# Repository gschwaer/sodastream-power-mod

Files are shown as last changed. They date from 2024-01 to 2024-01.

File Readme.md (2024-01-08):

# SodaStream Power Mod

> Because the Internet of Things needed a smart soda maker.

There is (or was) a soda maker called "SodaStream Power". It has some buttons and LEDs and uses a servo to do the usual pushing motion that soda makers require. Mine was broken probably due to an [unfortunate design decision](#just-why--the-beginnings) (and me). So I thought: If I have to fix it by replacing the MCU either way, why not use a WIFI-enabled one? So I build a replacement PCB with an ESP8266. It even runs python! 😲

Disclaimer: It doesn't access the internet. But it could! -- But what for? Maybe I should blink the current time in morse code for each new soda, or add a cloud backend so I can better scale my soda making. 🤔😉

So what does it use WIFI for? Well, I can debug it remotely while it's standing in the kitchen. 😅

Otherwise it just does, well, make soda. Though I improved (imo) the [user interface](#ui-changes) a little.

> ℹ️ I did this project in 2019, but I rewrote the software and documentation in 2023, so some details might be lost to time.

## Hardware

The PCB was designed in KiCad and fabricated by JLCPCB in 2019.

Main components:
* MCU: `ESP8266-12F`
* I2C-Port-Expander: `PCF8574AN`
  * Note: The suffix `A` implies a different I2C base address than the version without the `A`. The non-`A` chip works as well (but needs a minor change in code). (Took me a few hours debugging before I realized I stared at the wrong data sheet.)
* 2x Hall Switch: `SI7205-B-00-IV`
* High Side Power Switch: `TPS22810DBVR`

### Known Design issues

1. In the first revision I made a mistake and wired the LEDs to $V_{in} = 6.5 V$ (with higher values for the current limiting resistor). I thought this way I could prevent wasting power in the $3.3 V$ regulator for the LED current. Yes, that was dumb, because the regulator is a linear regulator, so the resistor dumps the same amount of power. 🤦 But the LEDs wouldn't burden the regulator at least. Anyway, the actual problem was that the port expander did not have open drain ports. Instead, ports are actively driven to low and high ($3.3V$), so in the "off" state, the LEDs (+Resistor) would see $6.5V-3.3V = 3.2V$ and would just be dimmer. 😬 I fixed it by cutting a trace and botching a wire to have the LEDs use the $3.3V$ supply rail. I'm still using that version to date. In the KiCad project that mistake has been fixed. But I didn't reorder a PCB, so that change is untested.
2. I used the least sensible GPIOs (GPIO 0, 2) for IO. It worked ok in the end, though I later had a minor issue in micropython with PWM on GPIO2 after a soft reset, because GPIO2 is a boot select pin. But I was able to fix that in software and either way: in regular operation we don't soft reset.
3. I placed some components and traces beside the antenna. Probably not good, but works ok. There is unfortunately not much space for traces around this huge center cutout.

### Schematics

> ⚠️ Warning: The [KiCad project](./PCB/Sodastream/) was converted from an older KiCad version. I'm not sure if that worked ok.

For ease of use I made some screenshots of the schematics.

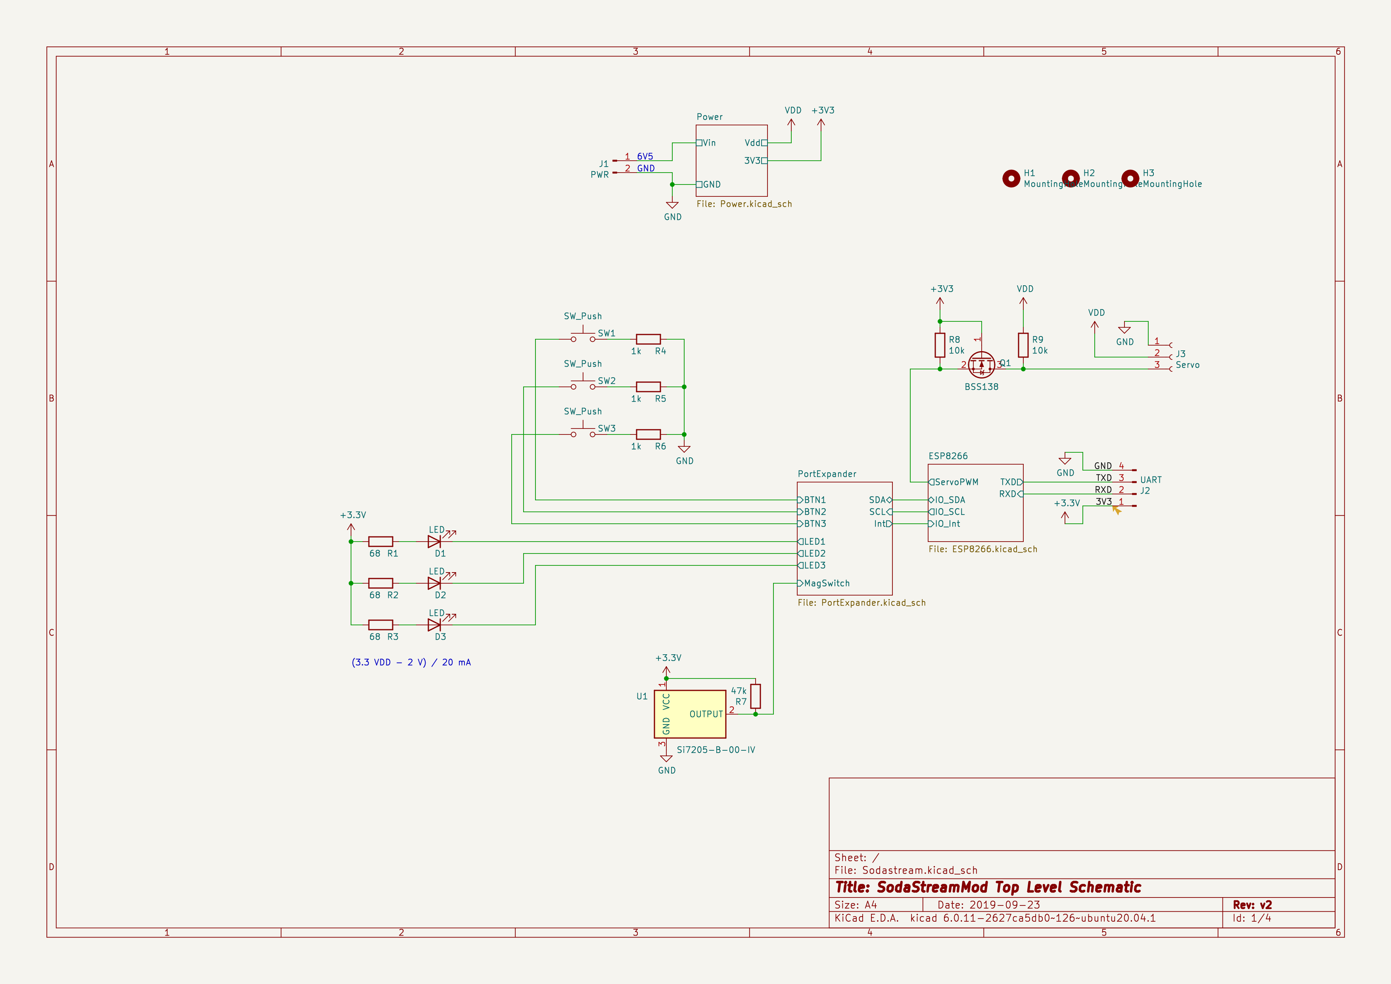
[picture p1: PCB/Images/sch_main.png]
main

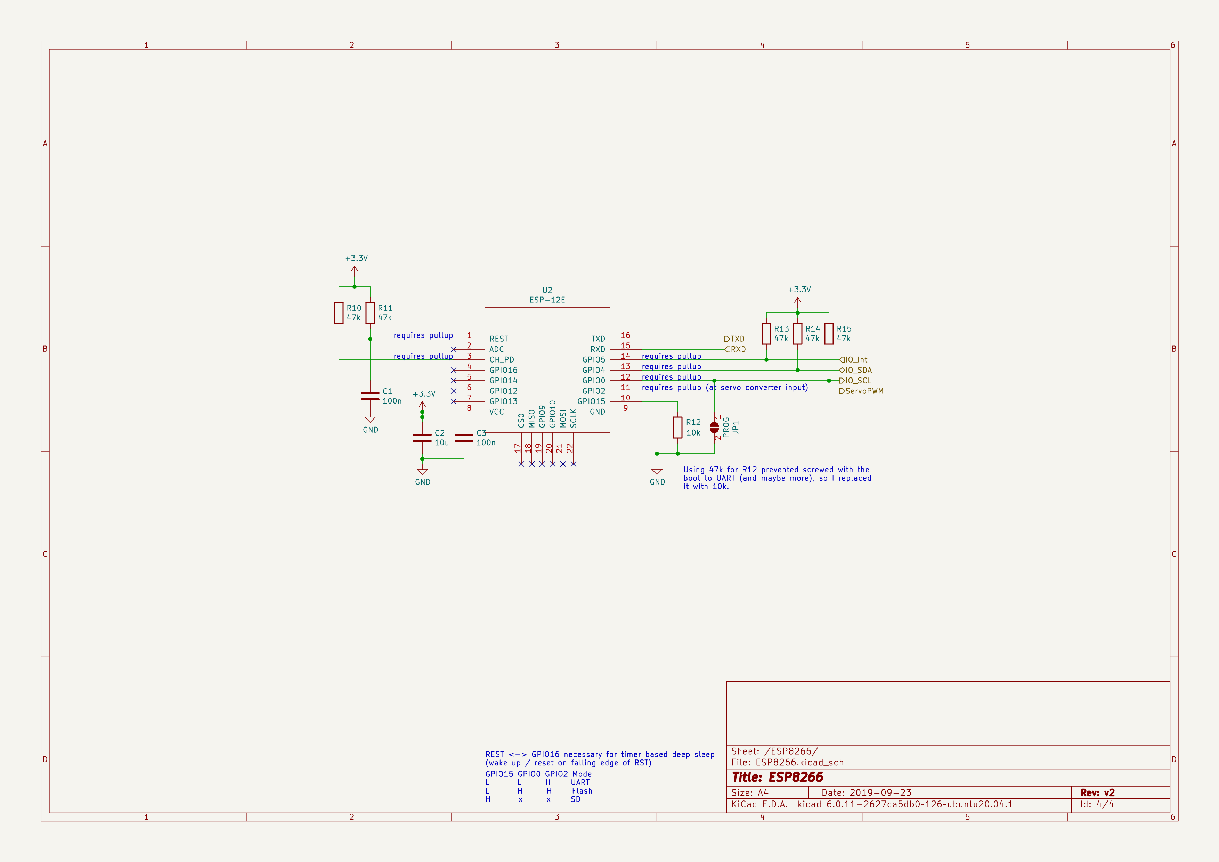
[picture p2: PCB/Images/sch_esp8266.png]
esp8266

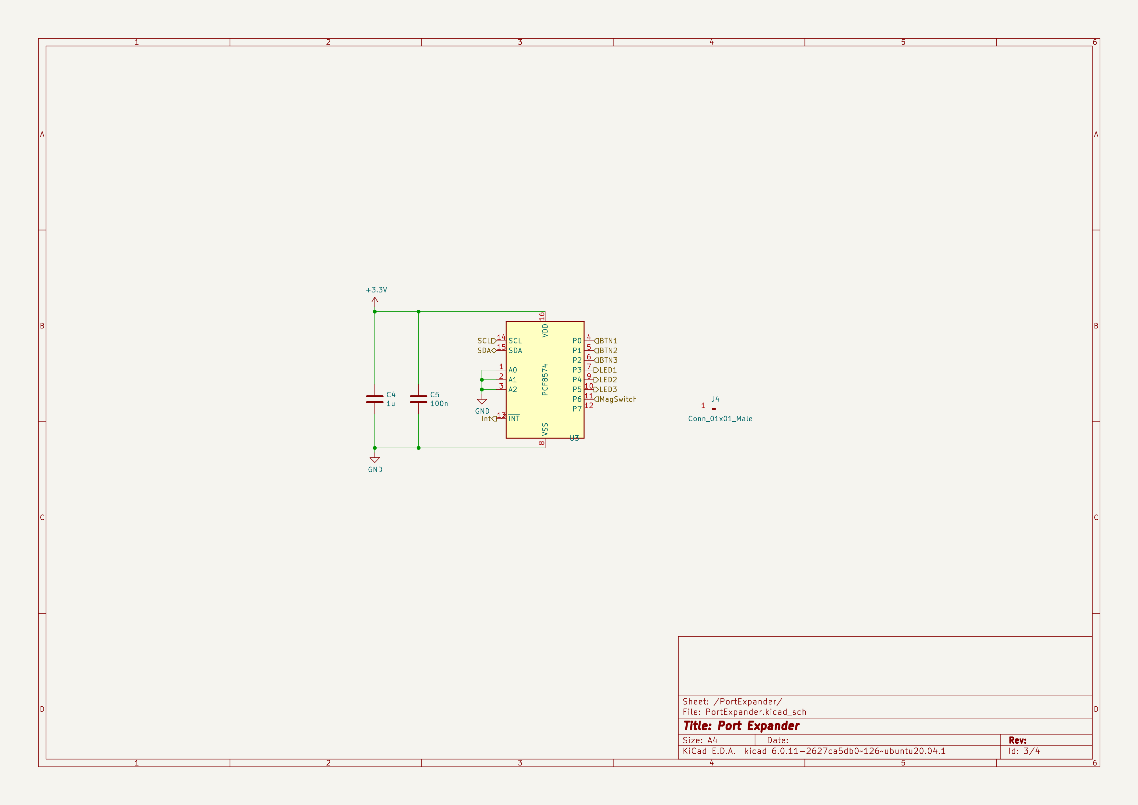
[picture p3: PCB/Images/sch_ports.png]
ports

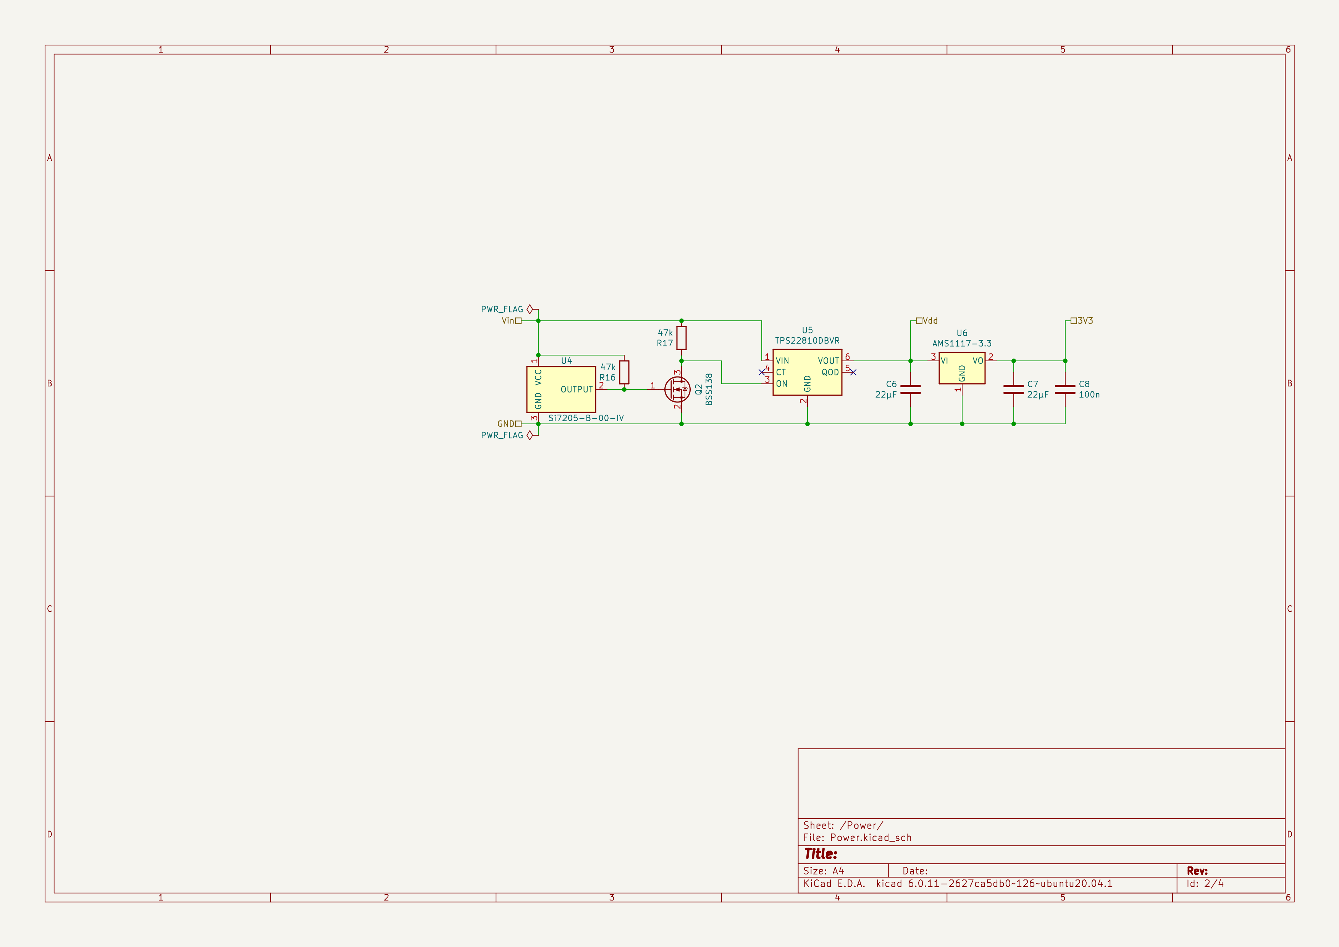
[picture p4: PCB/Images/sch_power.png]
power


### Layout

I measured the holes and cutouts on the original PCB and used identical ones on my PCB so it fits in the PCB holder. The pink areas are markings for special locations in the PCB housing: Left and right areas are keep out zones for the housing's snap fit hooks. The area in the center marks where the cabling leaves the water-proof housing.

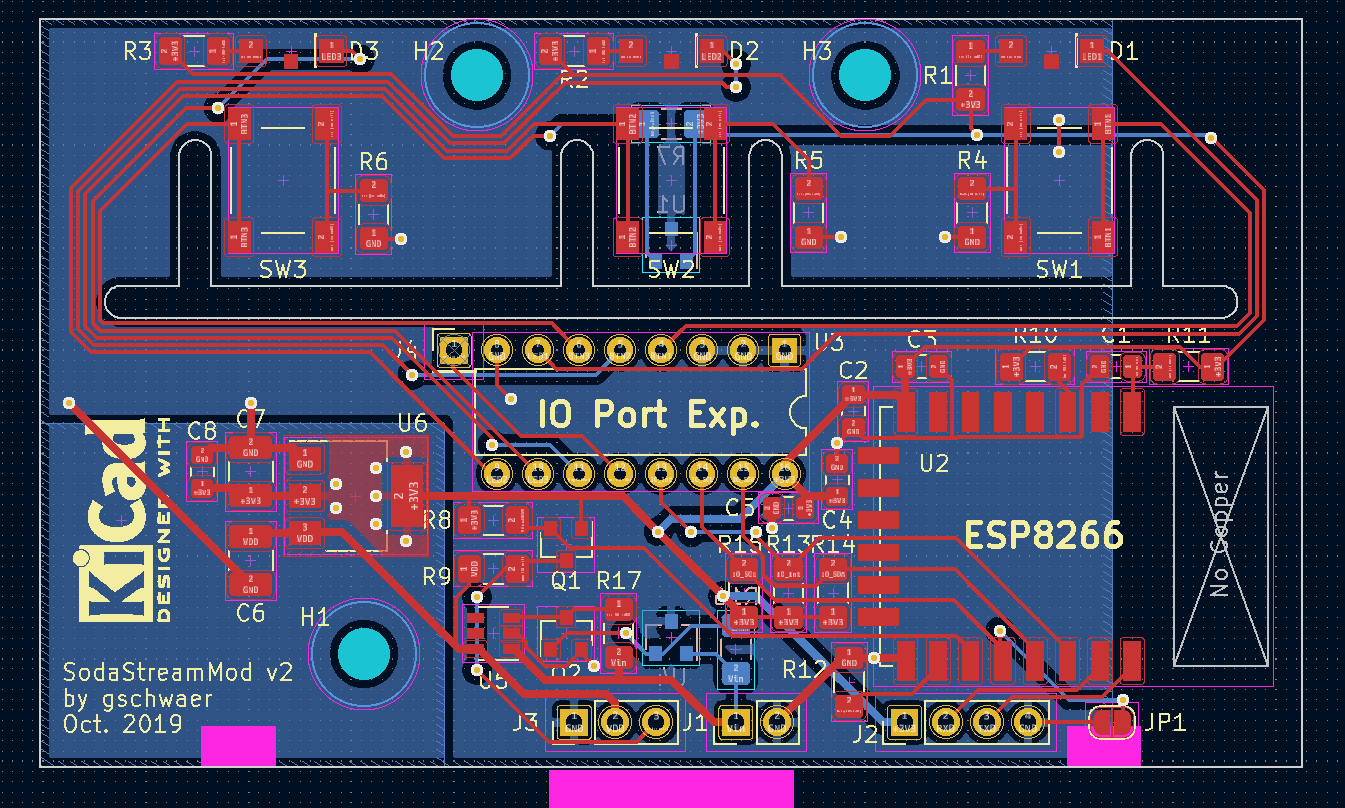
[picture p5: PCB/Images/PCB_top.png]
PCB_top

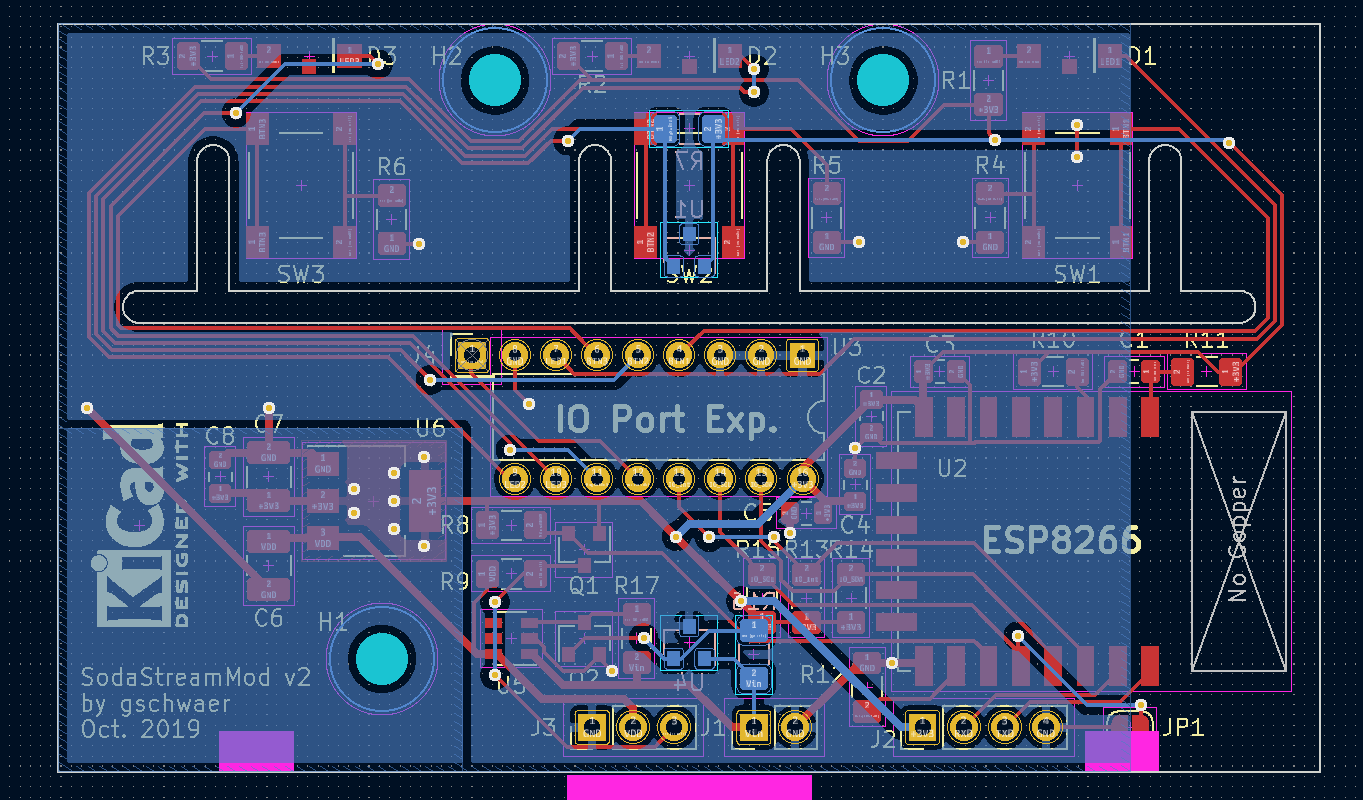
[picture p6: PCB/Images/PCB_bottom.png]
PCB_bottom

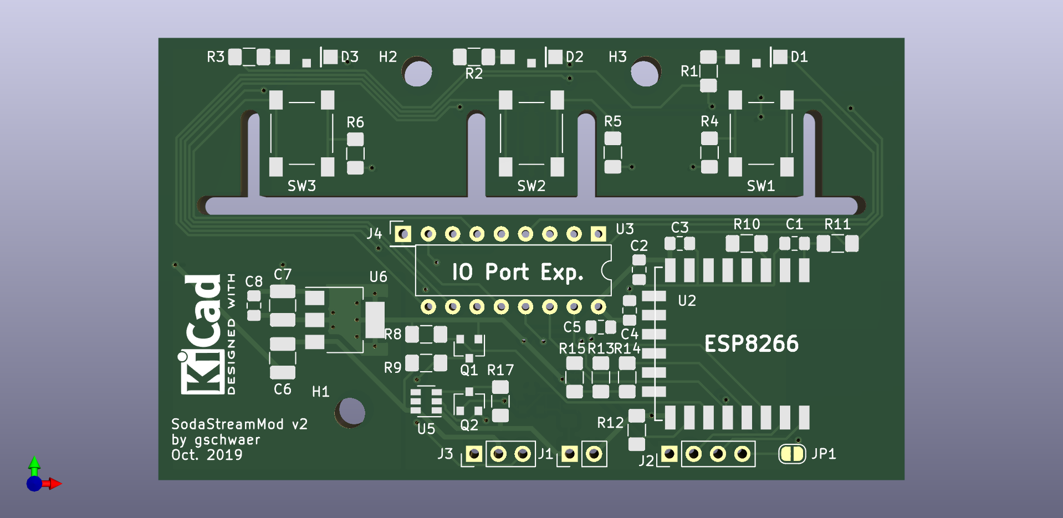
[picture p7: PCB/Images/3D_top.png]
render


## Software

This project uses [micropython](https://github.com/micropython/micropython/) version `1.20.0` installed as per the [documentation for ESP8266](https://docs.micropython.org/en/v1.20.0/esp8266/quickref.html). Here's the command I used:
```bash
esptool.py --port "${DEV}" --baud 460800 write_flash --erase-all --flash_size=detect 0 ESP8266_GENERIC-20230426-v1.20.0.bin
```
The code in [`./src`](./src/) is compiled with `make`. You need `mpy-cross`, `pyboard.py`, and `gcc` (see [`Makefile`](./src/Makefile)).

After that we can upload the code with [micropython's `pyboard.py` tool](https://docs.micropython.org/en/v1.20.0/reference/pyboard.py.html). The configs [`./src/webrepl_cfg.py`](./src/webrepl_cfg.py) and [`./src/wifi_cfg.py`](./src/wifi_cfg.py) require some adjustments.

After that, you can access the board via WiFi in the browser at http://192.168.0.123:8266/ (or which ever IP your board got, mDNS would be an improvement here, see [Future Work](#future-work)).

### UI Changes

Iirc the vendor UI was very basic: We have 3 buttons and 3 LEDs, when you insert a bottle all LEDs light up. Then you press one of the buttons, you get a low, medium, or high dose of CO2 into the bottle. The different doses are solely achieved by opening the CO2 valve for different, fixed durations.

Of course, that is reasonable, but it's actually a not much of an improvement compared to the manual soda makers. The main drawbacks are:
1. You still need to press a button,
2. when the CO2 cylinder empties, its pressure drops. This means the simple relationship between the duration of opening the valve and the applied CO2 dose does not hold anymore.

Drawback 1. is easily mitigated by beginning to open the CO2 valve as soon as a bottle is inserted. This means I cannot select the dose beforehand. This can be remedied by allowing a change of the dose *during* the operation. (This change is only in effect for the current soda making.)

I solved drawback 2. by tracking the cylinder state. I redefined the buttons to mean *left = "less CO2"*, *right = "more CO2"* (*center = "abort/restart"*). If a selection is made after the soda making is done, it is saved for next time. So when the CO2 cylinder empties, I can adjust the valve opening duration step by step whenever a bottle is not pressured to the degree I want. I also added some more subtle functions, and a debug mode:

| Button | Held Down Before* | Pressed While | Pressed After |
|---|---|---|---|
| left | (+right) reset cylinder state | less CO2 (temp) | less CO2 (saved) |
| right  | (+left) reset cylinder state  | more CO2 (temp) | more CO2 (saved) |
| middle | debug mode (WiFi) | abort | start again |

Table: Effect of buttons (1) held down while inserting a bottle, (2) pressed while the soda making happens, and (3) pressed after the soda making is completed. (* If any button is held down while a bottle is inserted, the CO2 valve stays closed. So resetting the cylinder state and entering debug mode can be done without wasting CO2.)

### Issues

I ran into some issues:

WebREPL:
* It's annoying to figure out the boards IP address. I currently check my router. But mDNS would be an obvious improvement.
* I regularly forget that when logging in via WebREPL, my python code is still running. Remember: after logging in, do `ctrl+c` to end the running program.

Boot Time:
* Boot time increases every time you overwrite a python file that is loaded at boot! I assume that has something to do with the flash filesystem trying to prevent wear. Maybe it does some copy-on-write with a linked list to traverse to the latest valid chunk? idk
  * If I remember correctly (! I didn't confirm it again !), you can reset this behavior by reformatting the flash (after that you have to reupload all files):
    ```python
    import uos
    from flashbdev import bdev
    uos.VfsLfs2.mkfs(bdev)
    vfs = uos.VfsLfs2(bdev)
    uos.mount(vfs, "/")
    ```
* I am using the following boot flow: `boot.py` -...-> `main.py` -> `sprudler.mpy`. That is mainly because `boot.py` and `main.py` cannot be compiled `.mpy` files. In `boot.py` I only put everything that I want done ASAP and `main.py` only `import`s the compiled `.mpy` file. I experimented a lot while trying to bring down boot time. I did not save the experiment results, but this solution got the best results for my use-case.
* The servo has three positions: (1) valve closed & bottle unlocked, (2) valve closed & bottle locked, (3) valve open & bottle locked. In `boot.py` I move the servo to the second (2) position. While the servo is moving to that position, we load the rest of the software and regular operation begins. This reduces the effective delay until operation begins.
* To optimize the compiled `.mpy` file, I experimented with regular global constants, constants marked with `const()`, and plain inserted constants. I'm not entirely sure what worked best, because while experimenting I also stumbled upon the issue above. Iirc boot time was best with inserted constants. So I stuck with that and added a preprocessor step using regular C preprocessor defines like `#define MY_CONST 123` in `sprudler.py`. (They get slightly garbled by the `black` formatter, but meh, I just undo this in the `Makefile`. Not elegant but works ok.)

WiFi AP:
* The WiFi AP does not work on my board with micropython `1.20.0`, so I disabled it (see [issue](https://github.com/micropython/micropython/issues/9226#issuecomment-1718269312)).
  * To prevent the board from boot looping after flashing, connect via serial and spam-paste the following into the terminal (including the newline):
    ```
    import network; network.WLAN(network.AP_IF).active(False)

    ```
    After some tries it will hit after the REPL becomes ready but before the AP is set up and the boot loop stops.

PWM:
* The servo is twitching if WiFi is enabled: The ESP8266 does not have hardware PWM outputs, so micropython does software PWM. WiFi will add a lot of load, which adds occasional lag on the software PWM timer handler. Ok for me, I only use WiFi in debug mode, where I can live with some servo twitching.

## Just Why?! / The Beginnings

Why am I doing this? Well, the electronics of my soda maker "broke", here's what happened:

The original circuitry has a tilt switch. It is just a conductive ball resting on two parallel wires, thus shorting the connection. The whole thing is in a black rectangular plastic housing with enough head room so the ball can slightly move upwards. If the PCB is flipped upside down the ball will fall away from the wires (now an open circuit) and the MCU will register that.

It turns out, if the device is on, you flip it upside down, and press any button, the MCU will go into an error state and blink the LEDs. Okay fine, maybe we just don't want our precious soda on the floor. But there is **no** way to get out of this error state! Not power cycling, no combination of button presses, short and long presses, with or without a bottle inserted, I tried everything I could think of. So ... this device just bricks itself? 🙃

Side note: If you are that kind of person (like me) who wants to know how devices work, and like to open them up to find out, you sometimes move parts aside, like for example **the PCB**, and maybe even let it dangle **upside down** on the side since the cables are so short...

However, I cannot be 100% certain that this is what bricked it. But there is a tilt switch on the PCB, it's connected to the controller, and the device went into the error state once I operated it with the PCB hanging upside down. But it could have been something else I did, who knows.

Why would the manufacturer do that? Not sure, maybe it is due to a regulation? CO2 in compressed gas cylinders is actually liquid. So from what I read, if you operate the valve while the CO2 cylinder is upside down it will spill the liquid CO2 which is very cold due to the drop in pressure. Maybe they wanted (or had) to prevent this hazard. (But why permanently!?)

## Future Work

- Add mDNS, so I don't need to look up the IP address.
  - https://github.com/vaudric/micropython/tree/main/mdns
  - https://github.com/nickovs/slimDNS
- Measure bottle pressure with a pressure sensor?

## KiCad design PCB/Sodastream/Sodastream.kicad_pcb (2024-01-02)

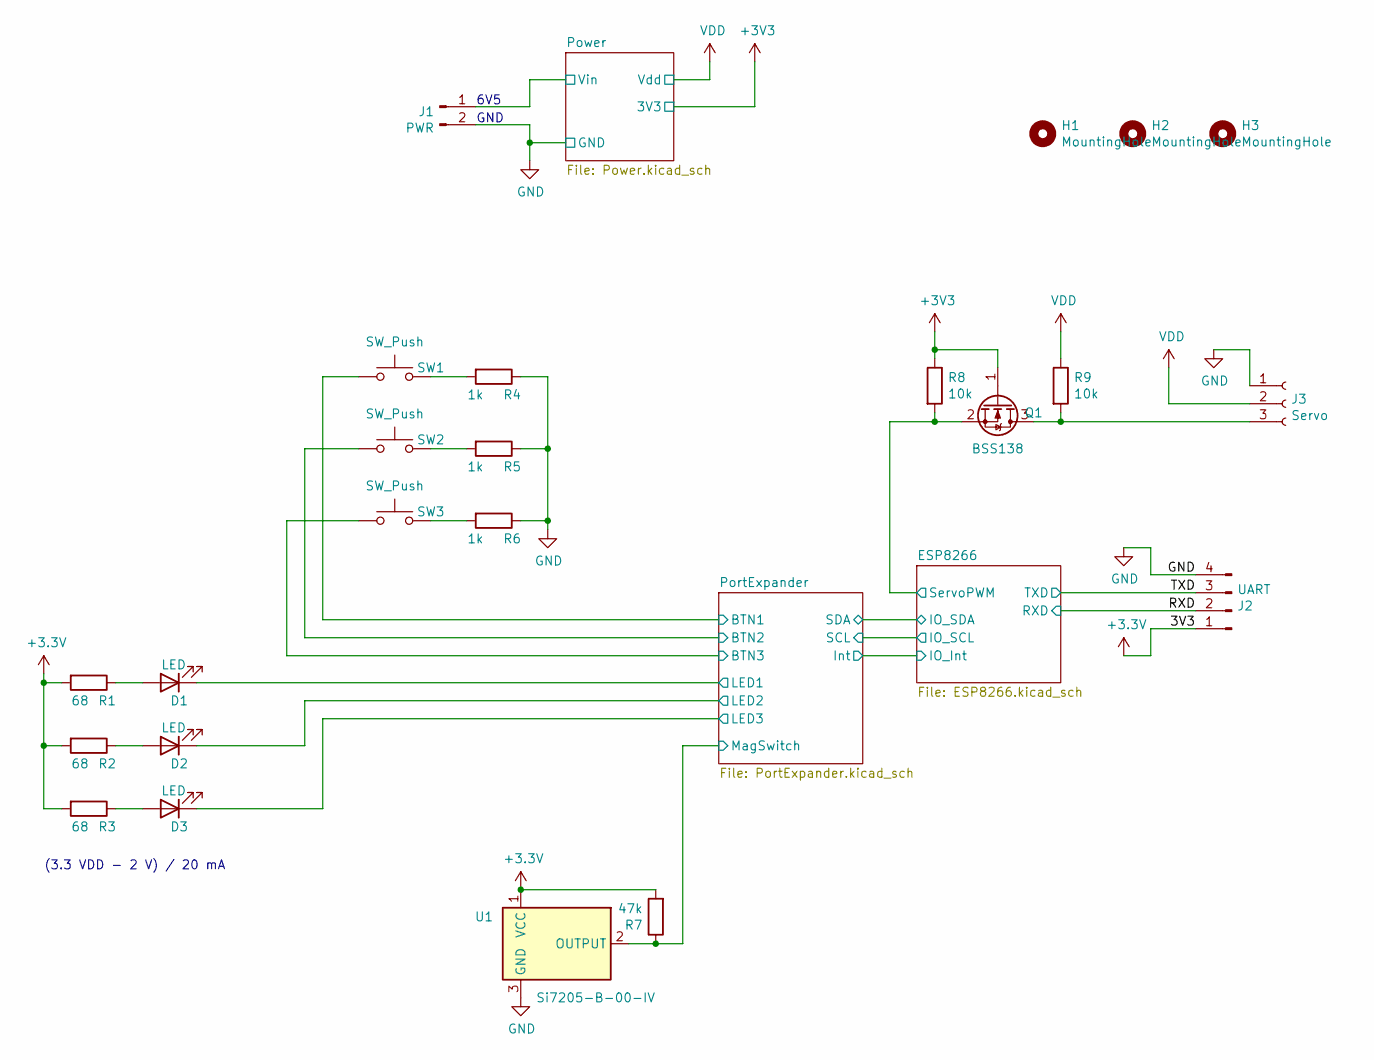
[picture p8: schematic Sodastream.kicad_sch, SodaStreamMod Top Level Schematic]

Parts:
D1, D2, D3: LED; LED_SMD_SideView_3.0x1.0x2.0_2+1pin
H1, H2, H3: MountingHole; MountingHole_3.2mm_M3
J1: PWR; PinHeader_1x02_P2.54mm_Vertical
J2: UART; PinHeader_1x04_P2.54mm_Vertical
J3: Servo; PinHeader_1x03_P2.54mm_Vertical
Q1: BSS138; SOT-23
R1, R2, R3: 68; R_1206_3216Metric_Pad1.42x1.75mm_HandSolder
R4, R5, R6: 1k; R_1206_3216Metric_Pad1.42x1.75mm_HandSolder
R7: 47k; R_1206_3216Metric_Pad1.42x1.75mm_HandSolder
R8, R9: 10k; R_1206_3216Metric_Pad1.42x1.75mm_HandSolder
SW1, SW2, SW3: SW_Push; SW_WE_6x6mm
U1: Si7205-B-00-IV; SOT-23

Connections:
+3V3: J2.1, Q1.1 (G), R1.2, R2.2, R3.2, R7.2, R8.1, U1.1 (VCC); also elsewhere on the board
/ESP8266/ServoPWM: Q1.2 (S), R8.2; also elsewhere on the board
/PortExpander/BTN1: SW1.1; also elsewhere on the board
/PortExpander/BTN2: SW2.1; also elsewhere on the board
/PortExpander/BTN3: SW3.1; also elsewhere on the board
/PortExpander/LED1: D1.1 (K); also elsewhere on the board
/PortExpander/LED2: D2.1 (K); also elsewhere on the board
/PortExpander/LED3: D3.1 (K); also elsewhere on the board
/PortExpander/MagSwitch: R7.1, U1.2 (OUTPUT); also elsewhere on the board
/Power/Vin: J1.1; also elsewhere on the board
/RXD: J2.2; also elsewhere on the board
/TXD: J2.3; also elsewhere on the board
GND: J1.2, J2.4, J3.1, R4.1, R5.1, R6.1, U1.3 (GND); also elsewhere on the board
unnamed: D1.2 (A), R1.1
unnamed: D2.2 (A), R2.1
unnamed: D3.2 (A), R3.1
unnamed: J3.3, Q1.3 (D), R9.2
unnamed: R4.2, SW1.2
unnamed: R5.2, SW2.2
unnamed: R6.2, SW3.2
VDD: J3.2, R9.1; also elsewhere on the board

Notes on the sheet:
(3.3 VDD - 2 V) / 20 mA
GND
6V5

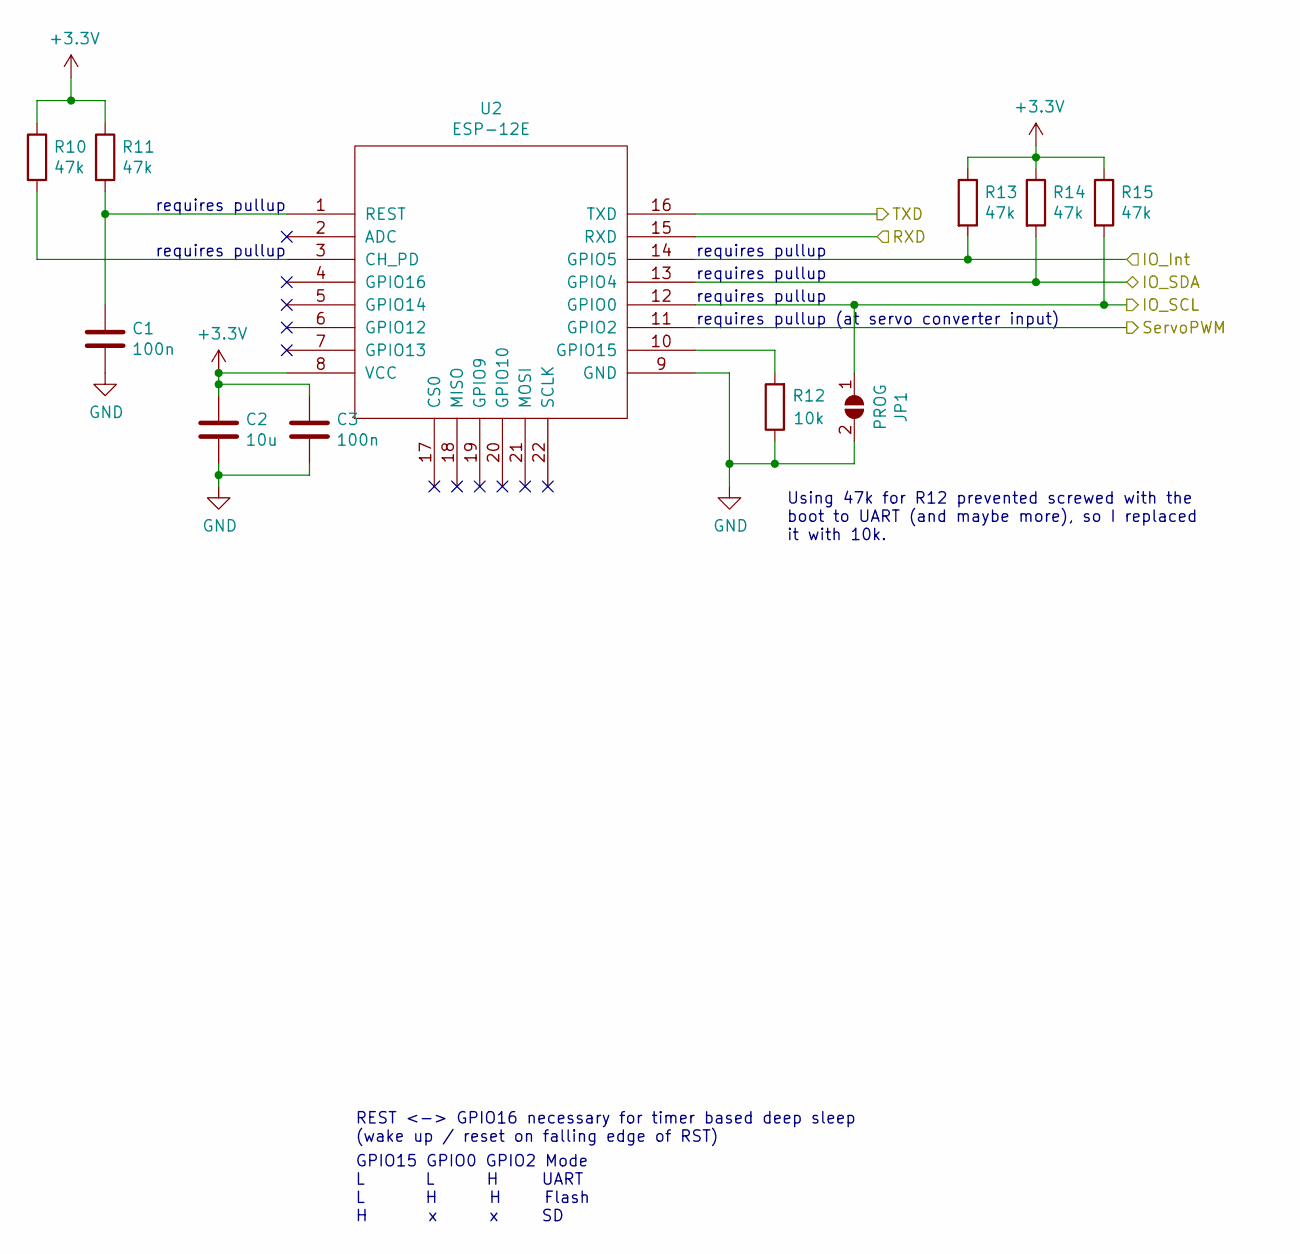
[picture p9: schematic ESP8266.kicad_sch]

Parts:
C1, C3: 100n; C_0805_2012Metric_Pad1.15x1.40mm_HandSolder
C2: 10u; C_0805_2012Metric_Pad1.15x1.40mm_HandSolder
JP1: PROG; SolderJumper-2_P1.3mm_Open_RoundedPad1.0x1.5mm
R10, R11, R13, R14, R15: 47k; R_1206_3216Metric_Pad1.42x1.75mm_HandSolder
R12: 10k; R_1206_3216Metric_Pad1.42x1.75mm_HandSolder
U2: ESP-12E; ESP-12E_SMD

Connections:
+3V3: C2.1, C3.1, R10.1, R11.1, R13.1, R14.1, R15.1, U2.8 (VCC); also elsewhere on the board
/ESP8266/IO_Int: R13.2, U2.14 (GPIO5); also elsewhere on the board
/ESP8266/IO_SCL: JP1.1 (A), R15.2, U2.12 (GPIO0); also elsewhere on the board
/ESP8266/IO_SDA: R14.2, U2.13 (GPIO4); also elsewhere on the board
/ESP8266/ServoPWM: U2.11 (GPIO2); also elsewhere on the board
/RXD: U2.15 (RXD); also elsewhere on the board
/TXD: U2.16 (TXD); also elsewhere on the board
GND: C1.2, C2.2, C3.2, JP1.2 (B), R12.1, U2.9 (GND); also elsewhere on the board
unnamed: C1.1, R11.2, U2.1 (REST)
unnamed: R10.2, U2.3 (CH_PD)
unnamed: R12.2, U2.10 (GPIO15)

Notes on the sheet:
requires pullup
requires pullup (at servo converter input)
Using 47k for R12 prevented screwed with the boot to UART (and maybe more), so I replaced it with 10k.
REST <-> GPIO16 necessary for timer based deep sleep (wake up / reset on falling edge of RST)
GPIO15 GPIO0 GPIO2 Mode L L H UART L H H Flash H x x SD

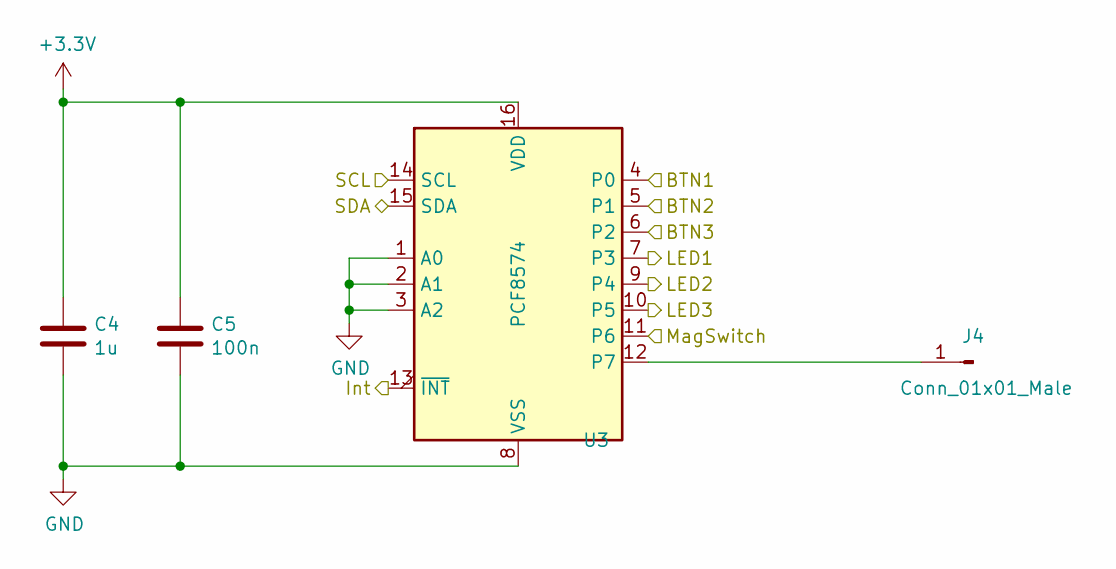
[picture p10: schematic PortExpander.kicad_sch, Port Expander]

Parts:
C4: 1u; C_0805_2012Metric_Pad1.15x1.40mm_HandSolder
C5: 100n; C_0805_2012Metric_Pad1.15x1.40mm_HandSolder
J4: Conn_01x01_Male; PinHeader_1x01_P2.54mm_Vertical
U3: PCF8574; DIP-16_W7.62mm

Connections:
+3V3: C4.1, C5.1, U3.16 (VDD); also elsewhere on the board
/ESP8266/IO_Int: U3.13 (~INT); also elsewhere on the board
/ESP8266/IO_SCL: U3.14 (SCL); also elsewhere on the board
/ESP8266/IO_SDA: U3.15 (SDA); also elsewhere on the board
/PortExpander/BTN1: U3.4 (P0); also elsewhere on the board
/PortExpander/BTN2: U3.5 (P1); also elsewhere on the board
/PortExpander/BTN3: U3.6 (P2); also elsewhere on the board
/PortExpander/LED1: U3.7 (P3); also elsewhere on the board
/PortExpander/LED2: U3.9 (P4); also elsewhere on the board
/PortExpander/LED3: U3.10 (P5); also elsewhere on the board
/PortExpander/MagSwitch: U3.11 (P6); also elsewhere on the board
GND: C4.2, C5.2, U3.1 (A0), U3.2 (A1), U3.3 (A2), U3.8 (VSS); also elsewhere on the board
unnamed: J4.1, U3.12 (P7)

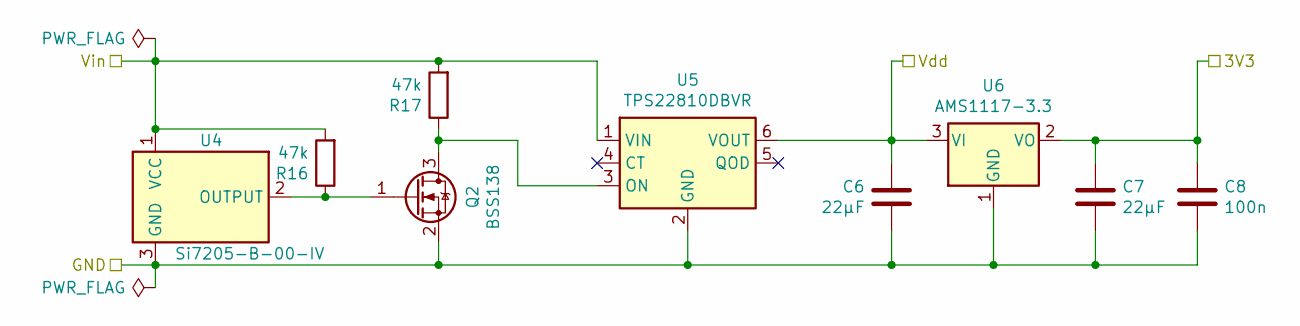
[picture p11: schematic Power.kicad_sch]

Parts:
C6, C7: 22µF; C_1210_3225Metric_Pad1.42x2.65mm_HandSolder
C8: 100n; C_0805_2012Metric_Pad1.15x1.40mm_HandSolder
Q2: BSS138; SOT-23
R16, R17: 47k; R_1206_3216Metric_Pad1.42x1.75mm_HandSolder
U4: Si7205-B-00-IV; SOT-23
U5: TPS22810DBVR; SOT-23-6
U6: AMS1117-3.3; SOT-223-3_TabPin2

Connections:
+3V3: C7.1, C8.1, U6.2 (VO); also elsewhere on the board
/Power/Vin: R16.2, R17.2, U4.1 (VCC), U5.1 (VIN); also elsewhere on the board
GND: C6.2, C7.2, C8.2, Q2.2 (S), U4.3 (GND), U5.2 (GND), U6.1 (GND); also elsewhere on the board
unnamed: Q2.1 (G), R16.1, U4.2 (OUTPUT)
unnamed: Q2.3 (D), R17.1, U5.3 (ON)
VDD: C6.1, U5.6 (VOUT), U6.3 (VI); also elsewhere on the board

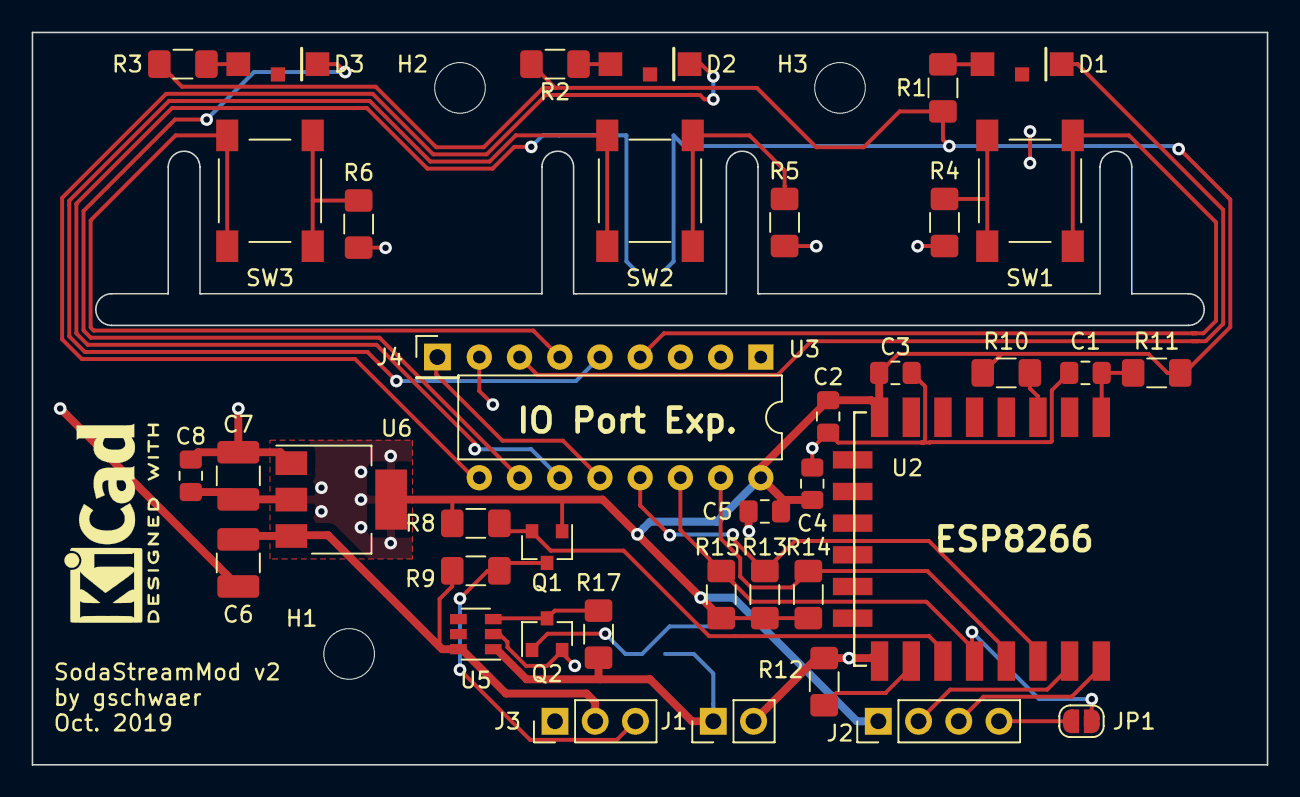
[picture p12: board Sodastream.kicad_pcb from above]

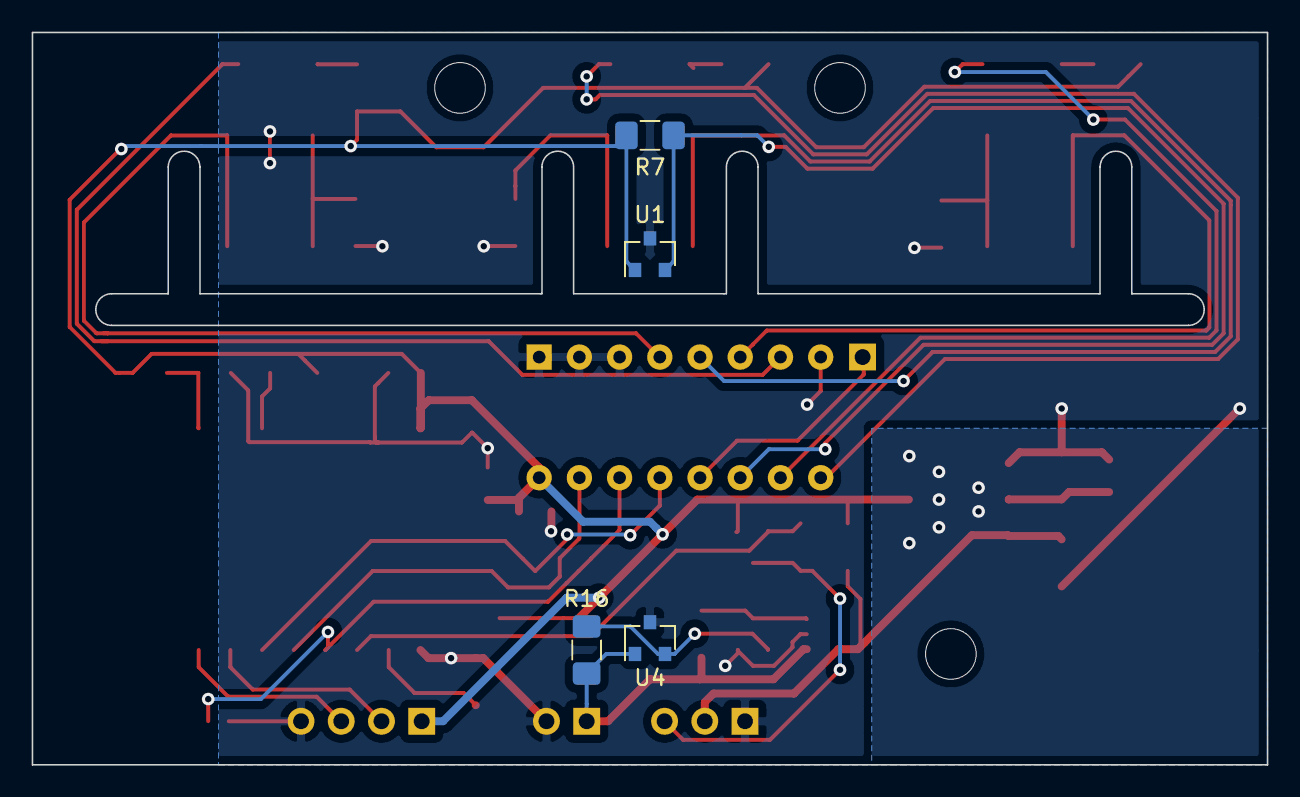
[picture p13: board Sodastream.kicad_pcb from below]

Board: 2 copper layers, 78.0 x 46.2 mm, 47 parts (4 on the bottom side), 30 nets.

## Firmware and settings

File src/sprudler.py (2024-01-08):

# Test with:
# ./pyboard.py -d /dev/serial/by-id/usb-1a86_USB_Serial-if00-port0 sprudler.py
# Build with:
# ../../micropython/mpy-cross/build/mpy-cross -march=xtensa -O3 ./sprudler.py
# Upload with:
# ./pyboard.py -d /dev/serial/by-id/usb-1a86_USB_Serial-if00-port0 -f cp sprudler.py :sprudler.py
# (beware, `import` prioritizes .py files over .mpy files)

import machine
import uasyncio
import time


# Setup servo

# define SERVO_PIN 2
# define SERVO_PWM_OPEN 50
# define SERVO_PWM_CLOSED 74
# define SERVO_PWM_ACTION 103

servo_pwm = machine.PWM(machine.Pin(SERVO_PIN), freq=50, duty=SERVO_PWM_CLOSED)
# servo_pwm.deinit()  # Workaround for broken PWM after soft-reset
# servo_pwm = machine.PWM(machine.Pin(SERVO_PIN), freq=50, duty=SERVO_PWM_CLOSED)


# Setup port extender

# define PORT_EXT_PIN_SCL 0
# define PORT_EXT_PIN_SDA 4
# define PORT_EXT_PIN_INT 5
# define PORT_EXT_I2C_FREQ 100000
# define PORT_EXT_I2C_ADDR 0b0111000
# define PORT_EXT_I2C_DFLT 0xFF

i2c = machine.I2C(
    scl=machine.Pin(PORT_EXT_PIN_SCL, machine.Pin.IN),
    sda=machine.Pin(PORT_EXT_PIN_SDA, machine.Pin.IN),
    freq=PORT_EXT_I2C_FREQ,
)
i2c_buf = bytearray(1)  # static buffer

# Setup button callback

# define BUTTON_LEFT 0
# define BUTTON_MID 1
# define BUTTON_RIGHT 2

btn_changed_flag = uasyncio.ThreadSafeFlag()
btn_pressed_mask = 0
btn_released_mask = 0


def button_callback(_pin):
    global btn_pressed_mask
    global btn_released_mask

    i2c.readfrom_into(PORT_EXT_I2C_ADDR, i2c_buf)
    btn_up_mask = i2c_buf[0] & 0x7
    # only buttons that were pressed are marked as now released
    btn_released_mask |= btn_up_mask & btn_pressed_mask
    btn_pressed_mask |= 0b111 ^ btn_up_mask  # same as ~btn_up_mask & 0x7

    btn_changed_flag.set()


ext_int = machine.Pin(PORT_EXT_PIN_INT, machine.Pin.IN)
ext_int.irq(trigger=machine.Pin.IRQ_FALLING, handler=button_callback)

# Setup LEDs
led_state = PORT_EXT_I2C_DFLT


def switch_leds(on_bits):
    global led_state

    led_state = (led_state & 0b11000111) | ((0b111 ^ on_bits) << 3)
    i2c_buf[0] = led_state
    i2c.writeto(PORT_EXT_I2C_ADDR, i2c_buf)


# Setup state

# define STATE_DEBUG -1
# define STATE_IDLE 0
# define STATE_ACTION 1
# define STATE_WAITING 2

state = STATE_IDLE
state_since = time.ticks_ms()
state_changed_event = uasyncio.Event()


def change_state(target_state):
    global state
    global state_since

    state = target_state
    state_since = time.ticks_ms()
    state_changed_event.set()
    state_changed_event.clear()


# Initial state
i2c.readfrom_into(PORT_EXT_I2C_ADDR, i2c_buf)
btn_up_mask = i2c_buf[0] & 0x7
if btn_up_mask == 0b111:  # no button pressed
    change_state(STATE_ACTION)
else:
    if btn_up_mask == 0b010:  # left and right button pressed
        import os

        try:
            os.remove("settings.cfg")
        except OSError:
            pass  # file does not exist

        switch_leds(111)
        time.sleep_ms(200)
        switch_leds(000)
        time.sleep_ms(200)
        switch_leds(111)
        time.sleep_ms(200)
        switch_leds(000)

        servo_pwm.duty(SERVO_PWM_OPEN)

        change_state(STATE_IDLE)
    else:  # middle button pressed
        change_state(STATE_DEBUG)

    # Wait until all buttons are unpressed
    while True:
        i2c.readfrom_into(PORT_EXT_I2C_ADDR, i2c_buf)
        btn_up_mask = i2c_buf[0] & 0x7
        if btn_up_mask == 0b111:  # no button pressed
            break

        time.sleep_ms(100)

    btn_pressed_mask = 0
    btn_released_mask = 0


# Coroutines


async def button_handler():
    global btn_pressed_mask
    global btn_released_mask
    global state
    global pump_dur_ms
    global strength

    while True:
        await btn_changed_flag.wait()

        if (1 << BUTTON_LEFT) & btn_released_mask & btn_pressed_mask:
            btn_pressed_mask &= ~(1 << BUTTON_LEFT)
            btn_released_mask &= ~(1 << BUTTON_LEFT)

            # print("Left button was pressed")

            if state == STATE_ACTION or state == STATE_WAITING:
                pump_dur_ms -= 200
            elif state == STATE_IDLE:
                if strength > 0:
                    strength -= 1
                    with open("settings.cfg", "wb") as f:
                        f.write(strength.to_bytes(1, "little"))
                        # kinda unclean but moving this into the led handler sucks
                        switch_leds(0b000)
                        await uasyncio.sleep_ms(300)
                        switch_leds(0b111)

        if (1 << BUTTON_MID) & btn_released_mask & btn_pressed_mask:
            btn_pressed_mask &= ~(1 << BUTTON_MID)
            btn_released_mask &= ~(1 << BUTTON_MID)

            # print("Middle button was pressed")

            if state == STATE_ACTION or state == STATE_WAITING:  # abort
                change_state(STATE_IDLE)
            elif state == STATE_DEBUG or state == STATE_IDLE:  # (re)start
                change_state(STATE_ACTION)

        if (1 << BUTTON_RIGHT) & btn_released_mask & btn_pressed_mask:
            btn_pressed_mask &= ~(1 << BUTTON_RIGHT)
            btn_released_mask &= ~(1 << BUTTON_RIGHT)

            # print("Right button was pressed")

            if state == STATE_ACTION or state == STATE_WAITING:
                pump_dur_ms += 200
            elif state == STATE_IDLE:
                if strength < len(strength_map) - 1:
                    strength += 1
                    with open("settings.cfg", "wb") as f:
                        f.write(strength.to_bytes(1, "little"))
                        # kinda unclean but moving this into the led handler sucks
                        switch_leds(0b000)
                        await uasyncio.sleep_ms(300)
                        switch_leds(0b111)


percentage_done = 0.0
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
